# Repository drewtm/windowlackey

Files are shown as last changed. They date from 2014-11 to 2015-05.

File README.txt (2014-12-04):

WINDOWLACKEY
a light-based automatic window blinds controller

If you want to build one of these exactly like I did, you will require:
  1x Arduino Pro Mini 5V https://www.sparkfun.com/products/11113
  1x sunkee light sensor board http://www.amazon.com/gp/product/B00CW82WZY/
  1x zitrades motor driver board http://www.amazon.com/gp/product/B00E6NIMAM/
  1x tiny motors http://www.amazon.com/gp/product/B009AQLDSS/
  2x 607 bearings http://www.amazon.com/gp/product/B00K85I51I/
  1x SPST switch http://www.amazon.com/dp/B00AKVBEN6
  1x power supply http://www.amazon.com/gp/product/B00KC9Z5Y0/
  1x DC power jack http://www.amazon.com/dp/B00CQMGWIO/
  1x m7 x 35mm long hex head bolt
  2x flat-head wood screws, 3mm to 4mm diameter by about 15mm long
  1x pan-head wood screw, 3mm to 4mm diameter by 20-25mm long
  
A website like www.mouser.com sells similar switches and DC power jacks for much cheaper, but you have to pay shipping.

It also requires my BH1750FVI Arduino library https://github.com/drewtm/BH1750FVI

You'll also need an FTDI cable, or access to one temporarily, to program the Arduino.

You can 3D print the plastic parts from the included STL files if you have the exact same type of blinds that I have.

The wiring in that case is done in-place with small solid-core wire (i used wire from an ethernet cable),
and the wires lock all the circuit boards together into the case.

The gears and motor are for a ball-chain type blinds mechanism, often found on vertical blinds.

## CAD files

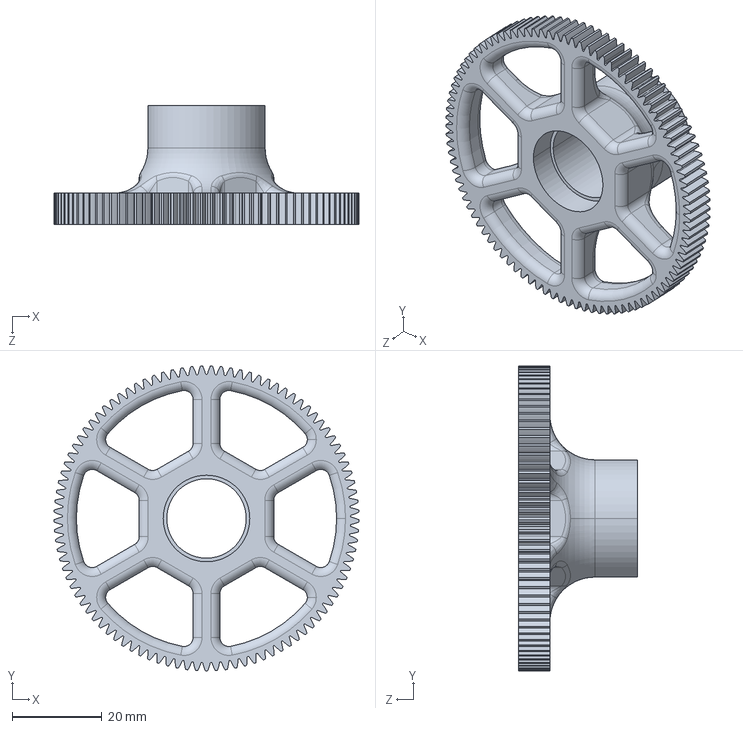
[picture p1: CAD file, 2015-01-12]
large gear without sprocket.STEP
68.0 x 68.0 x 26.5 mm

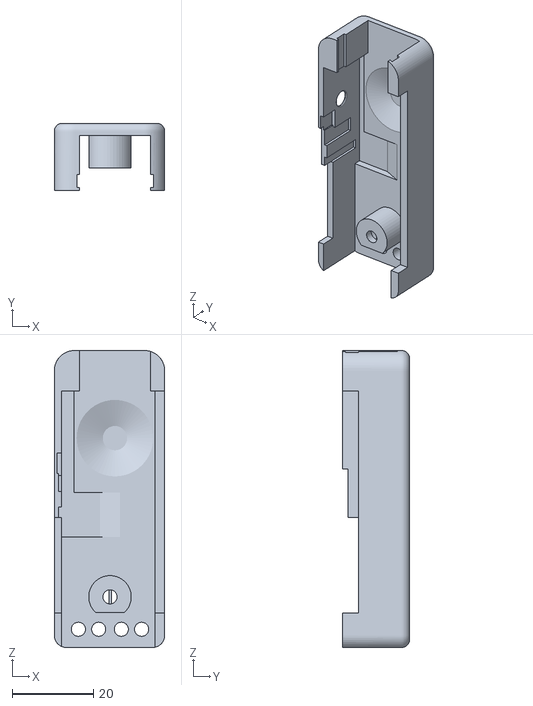
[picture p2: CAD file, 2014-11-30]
box lid.STL
27.2 x 16.7 x 73.3

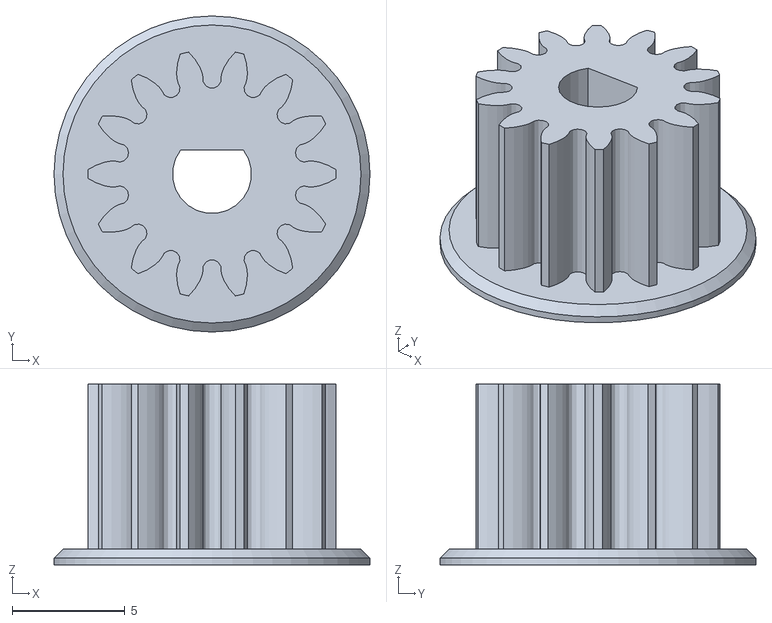
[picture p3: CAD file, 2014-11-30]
pinion gear.STL
14.0 x 14.0 x 8.00

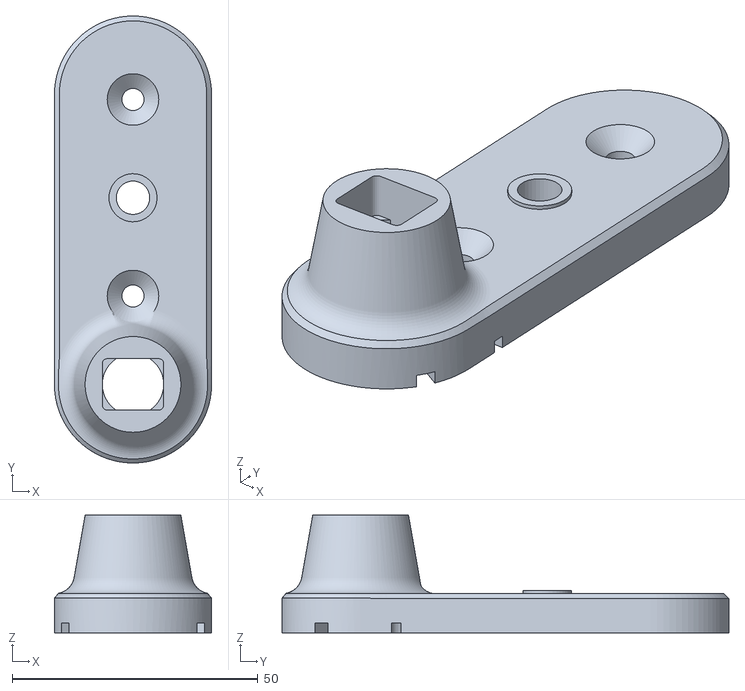
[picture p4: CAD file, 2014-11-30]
anchor bracket.STL
32.0 x 91.0 x 24.0

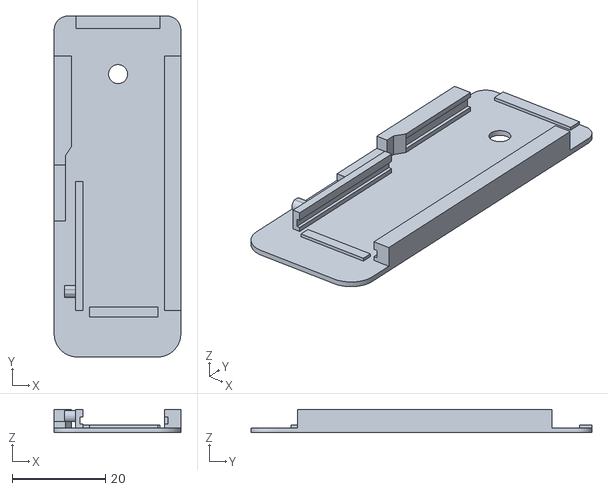
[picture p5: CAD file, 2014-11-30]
box base.STL
27.2 x 73.3 x 5.00

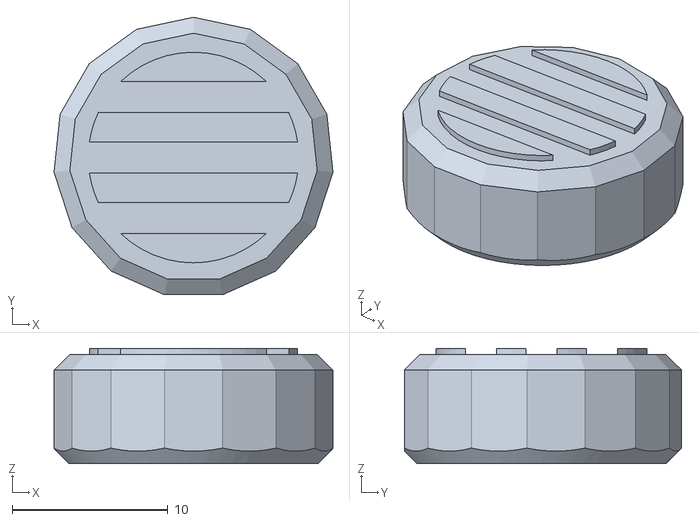
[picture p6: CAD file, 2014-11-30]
bolt knob.STL
17.9 x 17.8 x 7.40

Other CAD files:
large gear and sprocket.STL

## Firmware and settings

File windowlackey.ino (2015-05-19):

#include <Wire.h>
#include <BH1750FVI.h>
#include <EEPROM.h>

#define swpin 10    //pin that the override switch is connected to
#define motApin 7   //arduino pin for the motor driver 'A' input
#define motBpin 9   //arduino pin for the motor driver 'B' input
#define swON (digitalRead(swpin)==LOW) //a macro to read the switch (for easy polarity reversal)
#define CLOSETIME 16800  //how many milliseconds to drive when closing
#define OPENTIME 16500   //always open for a little less, to make sure it always gets all the way closed
#define driveopen() digitalWrite(motApin,LOW); digitalWrite(motBpin,HIGH)  //macros to drive motor
#define driveclose() digitalWrite(motBpin,LOW); digitalWrite(motApin,HIGH) //
#define drivestop() digitalWrite(motBpin,LOW); digitalWrite(motApin,LOW)   //
#define hours(x) ((unsigned long int)(1000)*60*60*(x))  //a macro to convert hours to ms
#define addrStat 400  //the EEPROM address to store the last known state of the blinds, for power outages
#define addrDawn 401  //the EEPROM address to store the last calibrated dawn light level (2 bytes)
#define addrDusk 403  //the EEPROM address to store the last calibrated dusk light level (2 bytes)
#define EEPROMclosed 180             //an arbitrary code for the EEPROM state
#define EEPROMopen (EEPROMclosed+1)  //
#define avgsize 64  //the window size for the moving average filter

BH1750FVI eye;            //create the light sensor object
boolean blindsareopen;    //stores the status of the blinds in memory
boolean switchhasbeenon;  //stores the last known switch state
unsigned long int lastdawn=(unsigned long int)0-hours(22); //the last dusk and dawn time in millis.
unsigned long int lastdusk=lastdawn;                       //they initialize as though they happened
                                                           //more than 22 hours before startup
word dawnbright = 55;  //brightness level for dawn trigger
word duskbright = 40;  //brightness level for dusk trigger
word warnbright = 15;  //warning window, for LED indicator to let you know they'll move soon
word previous[avgsize];//buffer of previous samples for moving average light level
byte idx = 0;          //index into 'previous' buffer
boolean daytime;       //stores whether or not it's currently daytime

void setup() {
  Wire.begin();                  //have to use Wire to use light sensor
  eye.begin(BH_Singh);           //start the light sensor in single-sample, half-scale mode
  pinMode(13,OUTPUT);            //set up pins
  digitalWrite(13,LOW);          //
  pinMode(motApin,OUTPUT);       //
  digitalWrite(motApin,LOW);     //
  pinMode(motBpin,OUTPUT);       //
  digitalWrite(motBpin,LOW);     //
  pinMode(swpin, INPUT_PULLUP);  //the override switch uses the internal pullups
  
  for(byte i=0; i<avgsize; i++){        //initialize the averaging buffer.
    eye.startSingleSample(BH_Singh);    //getting all these samples
    while(!eye.sampleIsFresh());        //will take a few seconds.
    previous[i] = eye.getLightLevel();  //
  }
  
  daytime = ( previous[avgsize] > ((dawnbright+duskbright)/2));  //initial guess at whether it's daytime
  byte savedstatus=EEPROM.read(addrStat); //see if there's a saved status in EEPROM
  boolean poweronasopen;              //stores the flag for whether powering on with blinds closed or open
  switchhasbeenon=swON;               //check to see if we've powered up with the switch 'on'
  if( (savedstatus==EEPROMopen) || (savedstatus==EEPROMclosed) ){
    poweronasopen=(savedstatus==EEPROMopen);   //if there's a valid code in EEPROM, use that for status
    dawnbright=EEPROM.read(addrDawn)<<8;       //also load both bytes of
    dawnbright+=EEPROM.read(addrDawn+1);       //dawn light level and
    duskbright=EEPROM.read(addrDusk)<<8;       //both bytes of
    duskbright+=EEPROM.read(addrDusk+1);       //dusk light level
  }                                            //
  else{                                        //otherwise, this is probably the first powerup,
    poweronasopen=swON;                        //so the user has indicated whether the blinds are open
                                               //or closed by setting the switch appropriately
    EEPROM.write(addrDusk, byte(duskbright>>8)); //also, make sure that we store
    EEPROM.write(addrDusk+1, byte(duskbright));  //the default dusk/dawn brightness
    EEPROM.write(addrDawn, byte(dawnbright>>8)); //levels into EEPROM for the future
    EEPROM.write(addrDawn+1, byte(dawnbright));  //(two bytes each, just in case)
  }
  if(poweronasopen){
    blindsareopen=true;                        //remember that the blinds are open
    if(!daytime){                              //but if they need to close,
      closeblinds();                           //then close them
      lastdawn=millis()-hours(19);             //prevent immediate close/open cycle at startup
    }
  }
  else{
    blindsareopen=false;                       //opposite of above
    if(daytime){                               //
      openblinds();                            //
      lastdusk=millis()-hours(19);             //
    }
  }
  
}

void loop() {

  processBrightness();   //all the code is below in functions
  processSwitch();       //
  
}

void openblinds(){
  if(blindsareopen) return;    //never try to open blinds that are already open
  unsigned long int started, current, elapsed; //timing variables
  started=millis();              //note the current time
  driveopen();                   //turn on the motor
  do{
    current=millis();            //keep checking the time
    elapsed=current-started;     //
  }while(elapsed<OPENTIME);      //and seeing whether the motor has run long enough
  drivestop();                   //turn off the motor
  blindsareopen=true;            //record in RAM that the blinds are now open
  EEPROM.write(addrStat,EEPROMopen); //record in EEPROM
}

void closeblinds(){ //same as above, but for different length of time and motor direction
  if(!blindsareopen) return;
  unsigned long int started, current, elapsed;
  started=millis();
  driveclose();
  do{
    current=millis();
    elapsed=current-started;
  }while(elapsed<CLOSETIME);
  drivestop();
  blindsareopen=false;
  EEPROM.write(addrStat,EEPROMclosed);
}

void processBrightness(){
  
  eye.startSingleSample(BH_Singh);      //start a new light sample
  while(!eye.sampleIsFresh());          //wait for it to finish
  previous[idx] = eye.getLightLevel();  //replace a sample into the buffer at the current index
  
  unsigned long int sum = 0;
  for(byte i=0; i<avgsize; i++) sum += (unsigned long int)previous[i];
  sum = sum/avgsize;                    //create an average of the entire buffer window
  
  if(daytime){ //do the following if we're checking for it to get dark out
    if(previous[idx] < duskbright+warnbright) digitalWrite(13, HIGH); //light the warning LED if the most
    else digitalWrite(13, LOW);                                       //recent sample is almost dark
    unsigned long int timesincedusk = millis()-lastdusk; //calculate time since last dusk triggered
    if(timesincedusk > hours(20)){ //this forces dusk to be close to the same time of day as yesterday
      if((word)sum < duskbright){  //check the brightness only if it's been almost a whole day
        if(lastdusk==lastdawn) lastdawn=millis()-hours(19); //prevent immediate close/open cycle at startup
        lastdusk=millis();  //record the time, because this is today's dusk
        daytime = false;    //record that it is now night-time, to prevent this code from running for a while
        closeblinds();      //run the blinds closed
      }
    }
  }
  else{ //do the following if we're checking for it to get light out. same as above with different variables
    if(previous[idx] > dawnbright-warnbright) digitalWrite(13, HIGH);
    else digitalWrite(13, LOW);
    unsigned long int timesincedawn = millis()-lastdawn;
    if(timesincedawn > hours(20)){
      if((word)sum > dawnbright){
        if(lastdusk==lastdawn) lastdusk=millis()-hours(19);
        lastdawn=millis();
        daytime = true;
        openblinds();
      }
    }
  }
  
  idx++;                        //increase the buffer index because this sample round is over
  if(idx >= avgsize) idx=0;     //(circular buffer)
  
}

void processSwitch(){   //this is an edge trigger for the switch
  if(switchhasbeenon){  //so it only does something at the moment when you flip it
    if(!swON){
      closeblinds();
      if(swON){                          //if the switch is on now, it has been immediately turned back on
        eye.startSingleSample(BH_Singh); //which indicates that you're trying to train the closing time
        lastdusk = millis();             //so act as though this was a real dusk event
        daytime = false;                 //but also adjust the light trigger level
        while(!eye.sampleIsFresh());
        duskbright = (eye.getLightLevel()+duskbright)/2;
        EEPROM.write(addrDusk, duskbright>>8);
        EEPROM.write(addrDusk+1, byte(duskbright));
      }
      else switchhasbeenon=false;
    }
  }
  else{
    if(swON){
      openblinds();
      if(!swON){                         //training case (see above)
        eye.startSingleSample(BH_Singh); // start a new sample
        lastdawn = millis();             // record time
        daytime = true;                  // set daytime
        while(!eye.sampleIsFresh());     // wait for the light sample to be ready
        dawnbright = (eye.getLightLevel()+dawnbright)/2; //average the new trigger level with the old one
        EEPROM.write(addrDawn, byte(dawnbright>>8));
        EEPROM.write(addrDawn+1, byte(dawnbright));
      }
      else switchhasbeenon=true;
    }
  }
}

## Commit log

2014-11-30 added STL files
    added all the plastic parts for the case and mechanism, and updated
    README to match
    [anchor bracket.STL, bolt knob.STL, box base.STL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]
2014-12-02 comments and a bug fix
    commented code and fixed a possible error where the blinds would
    immediately open after closing the first time, if the blinds themselves
    change the light level hitting the sensor.
    [windowlackey.ino]
2014-12-02 forgot switch
    added the switch to the materials list in the README
2014-12-02 more README and a re-fix
    didn't fix the startup bug properly last time. README file is expanded;
    added the power supply and FTDI cable.
    [windowlackey.ino]
2014-12-04 DC power jack
    added DC power jack to materials list, with a note about sourcing the
    cheap electronics components
2014-12-04 add training functionality and re-re-fix
    added open/close trigger level training feature, via manual override
    switch. to train the dusk trigger level, close the blinds then flip the
    switch immediately back on before they're done closing. to train the
    dawn trigger level, do the reverse. also moved the 'prevent immediate
    close/open cycle' fix to the setup routine, which is where it needed to
    be.
    [windowlackey.ino]
2014-12-04 add screws and wiring diagram
    added the screws to the parts list and created a wiring diagram
2014-12-04 more startup tweaking
    the re-re-fix and the re-fix were both partially correct, as i now
    understand.
    [windowlackey.ino]
2015-01-12 added non-triangulated version of large gear
    Added non-triangulated version of the large gear without any sprocket,
    for modification in other CAD software to support alternative ball chain
    sizes.
    [large gear without sprocket.STEP]
2015-05-19 now stores tuning values in EEPROM
    Updated startup routine and switch triggering code to store tuned
    open/close brightness trigger levels in EEPROM so that you don't have to
    re-tune everything whenever the power goes out
